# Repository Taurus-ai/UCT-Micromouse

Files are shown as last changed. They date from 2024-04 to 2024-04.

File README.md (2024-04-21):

# UCT-Micromouse
Background
This repository contains the work for the Micromouse Project in the EEE3088F course for 2024. The goal is to design and build two critical subsystems for a maze-solving robot called a micromouse: the power module and the sensing module.

The power module is responsible for powering the robot's motors, charging the battery, and managing power efficiently. It ensures the micromouse has the energy it needs to navigate the maze.

The sensing module acts as the "eyes" of the micromouse, detecting obstacles, walls, and potential paths through the maze using sensors. Without accurate sensing, the robot would be unable to map and solve the maze effectively.

The main challenge of the project will be to adhere to a strict budget.

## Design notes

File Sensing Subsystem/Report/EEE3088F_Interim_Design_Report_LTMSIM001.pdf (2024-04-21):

# Chapter 1

# Subsystem Design

### 1.1 Design Decisions

### 1.1.1 Final Design

The final design is centred around the working of two circuits; the IR-emitter circuit and the IR-receiver circuit, (in order to meet SP04.)
Various configurations were considered for the IR-receiver circuit, particularly configurations involving photo-diodes and photo-transistors. Their trade-offs were compared, and the photo-transistor configuration was chosen.

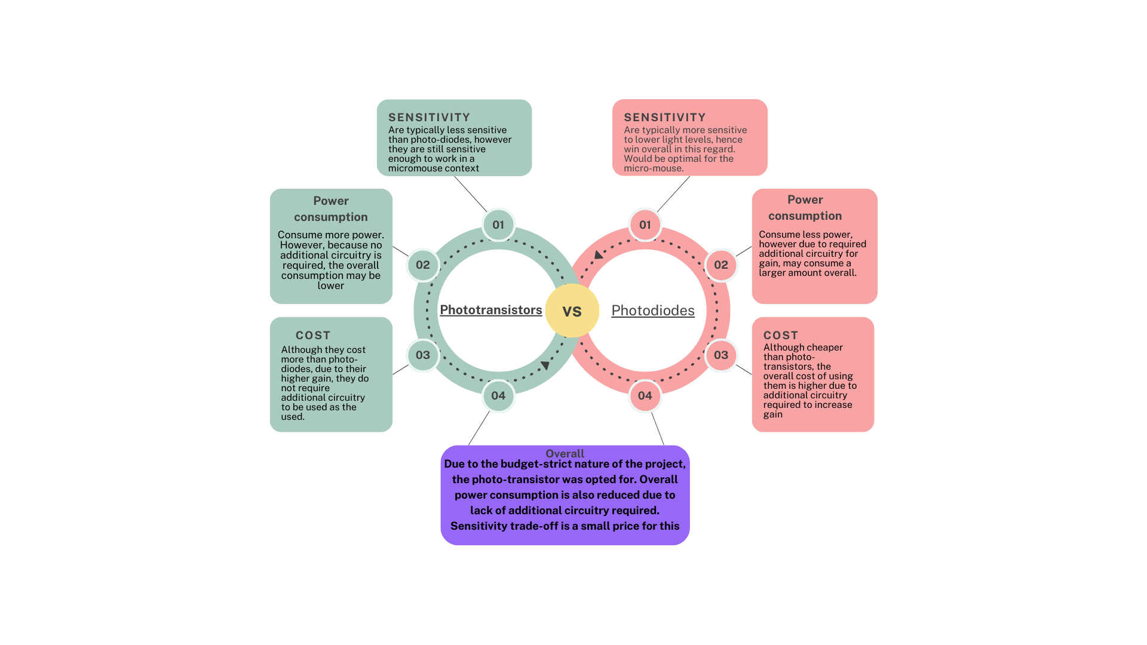
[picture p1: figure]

Figure 1.1: Comparison between phototransistor and photodiode

The choice was made to use the L-51ROPT1D1 phototransistor and OSRAM SFH-4544 IR-LED specifically was due to their spectral matching(940nm), which will ensures maximum signal strength, sensitivity and responsivity as both the receiver and the emitter will be operating at the same wavelengths.

In order to meet SP06 and UR02, the unique design decision to make use of a transistor to act as a switch within the IR-emitter circuit design was made.It will ensure that IR signals are only emitted once a command is given by the MCU, hence allowing for power saving functionality (through the use

1.1. Design Decisions

of code), as well as greater overall control of the circuit.
The decision to use a MOSFET as opposed to the other types of transistors was made due to faster switching speeds, lower conduction losses, and simpler drive circuitry. The drawback was that they are more prone to damage caused by electrostatic charges.
To align with the budget-strict nature of the project, the AO3401A MOSFET P-CH SOT23-3L was chosen.

Capacitors were incorporated into the design in order to stabilize the supply voltage (remove noise) as well as to reduce the turn time on the IR-emitter circuit. These proved to be reasonable trade-offs for the increase in overall cost that they posed. Even then, cheaper capacitors were used to save money.

For saved cost, surface mount resistors were chosen instead of through hole resistors (which are more expensive). The trade off was that these types of resistors are harder to remove and replace from the PCB, which may make things harder to fix if values were miscalculated.

Resistor values were calculated in the figure below:

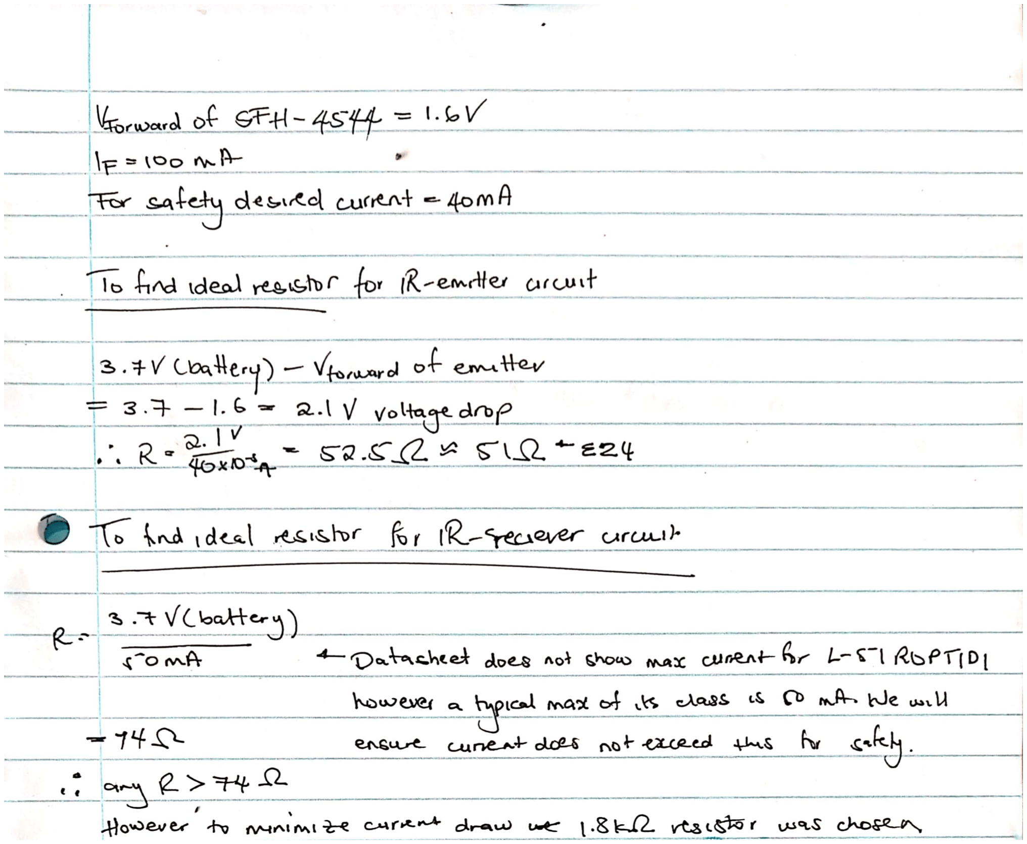
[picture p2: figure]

Figure 1.2: Resistor Value Calculations

If these resistor values are replaced with others, it may result in damage of components on one extreme (too low) or higher current draw on the other extreme, which may cause increased power consumption and hinder UR04.

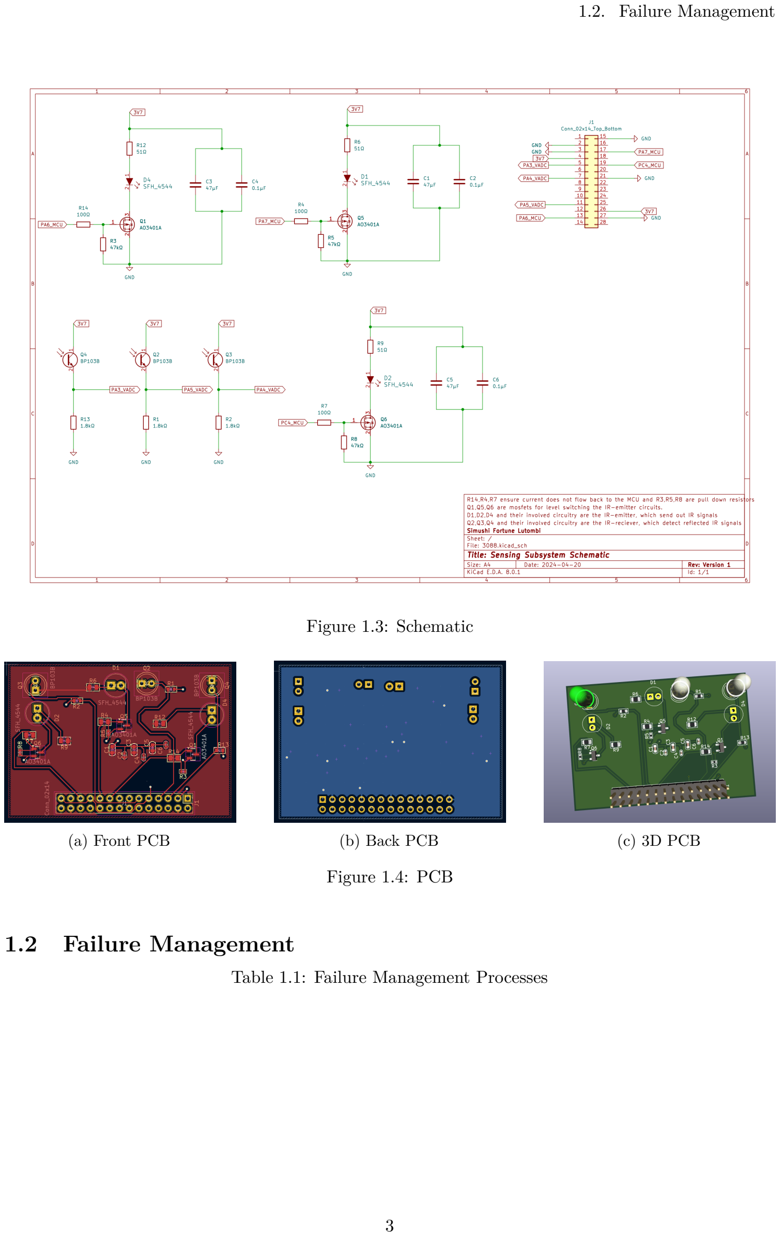
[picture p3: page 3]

1.2. Failure Management

Figure 1.3: Schematic

(a) Front PCB | (b) Back PCB | (c) 3D PCB

Figure 1.4: PCB

### 1.2 Failure Management

Table 1.1: Failure Management Processes

1.3. System Integration and Interfacing
Name | Description
Non-right angle traces | 90° traces were generally avoided to reduce the formation of acid traps during etching
Protective resistors | Various resistors were used to mitigate excessive current from flowing to
| components
Simulation of electrical circuit | The working of the electrical logic of the PCB was tested using Ki-cads inbuilt
ERC functions to ensure that there were no errors in this regard
Design logic testing | Ki-cads inbuilt Design Rule Checking functionality was used to
ensure that there were no obvious design faults, such as short circuits

### 1.3 System Integration and Interfacing

To integrate the subsystem with the rest of the system ....

Table 1.2: Interfacing specifications

Interface | Description | Pins/Output

I001

Sensing Submodule to Microcontroller(MC) for data transfer

- Pin7 to MC-PA4(GPIO)
- Pin11 to MC-PA5(GPIO)
- Pin5 to MC-PA3(GPIO)
- Pin13 to MC-PA6(GPIO)
- Pin17 to MC-PA7
- Pin19 to MC-PC4
- Pin2 to MC-GND
- Pin3 to MC-GND
- Pin15 to MC-GND
- Pin21 to MC-GND
- Pin27 to MC-GND
- Pin4 to MC-Battery
- Pin26 to MC-Battery

1.3. System Integration and Interfacing

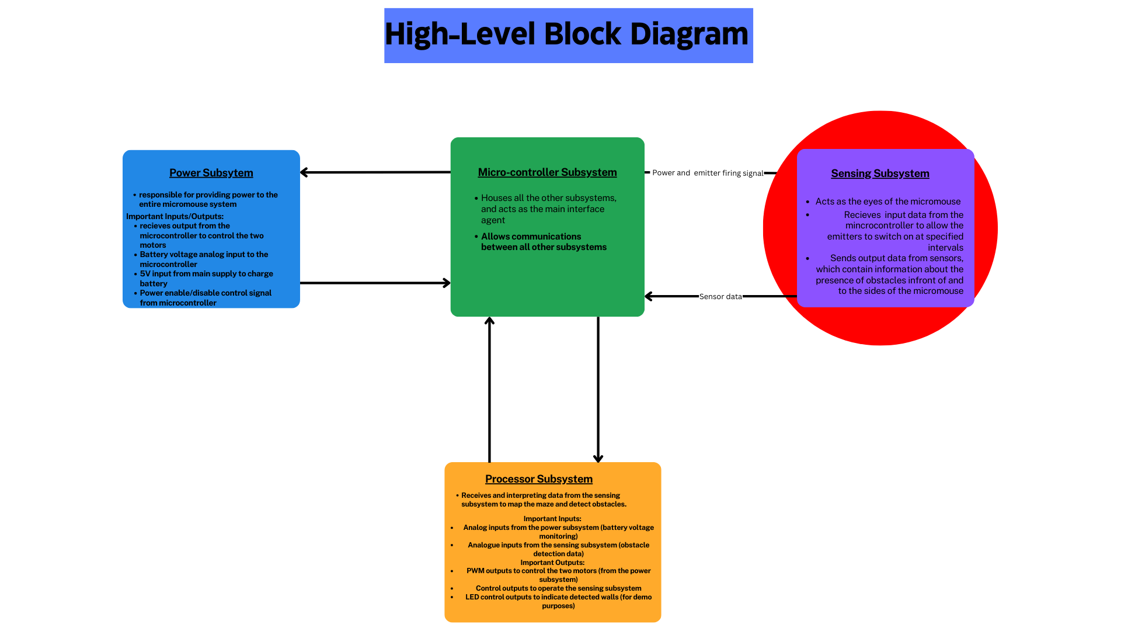
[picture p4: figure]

Figure 1.5: High-level Block Diagram

# Bibliography

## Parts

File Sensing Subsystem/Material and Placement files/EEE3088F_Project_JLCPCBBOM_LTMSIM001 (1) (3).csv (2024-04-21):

Comment | Designator | Footprint | JLCPCB Part #（optional）
P Channel SOT-23 MOSFET | Q1,Q5,Q6 | BP103B | C15127
940nm 5mm Infrared (IR) LED | D1,D2,D4 | AO3401A | C2900370
Thick Film Resistor ±1% 1.8kΩ | R1,R2,R13 | R_0603 | C4177
Thick Film Resistor ±1% 51Ω | R6,R12,R9 | R_0805 | C17738
4.7uF ±20% Multilayer Ceramic Capacitors | C1,C3,C5 | C_0603 | C23733
100nF ±10% Multilayer Ceramic Capacitors | C2,C4,C6 | C_0402 | C14663
Thick Film Resistor ±1% 47kΩ | R3,R5,R8 | R_0402 | C25792
Thick Film Resistors ±1% 100Ω | R4,R14,R7 | R_0805 | C17408
940nm 5mm Phototransistor | Q2,Q3,Q4 | SFH_4544 | C2962773

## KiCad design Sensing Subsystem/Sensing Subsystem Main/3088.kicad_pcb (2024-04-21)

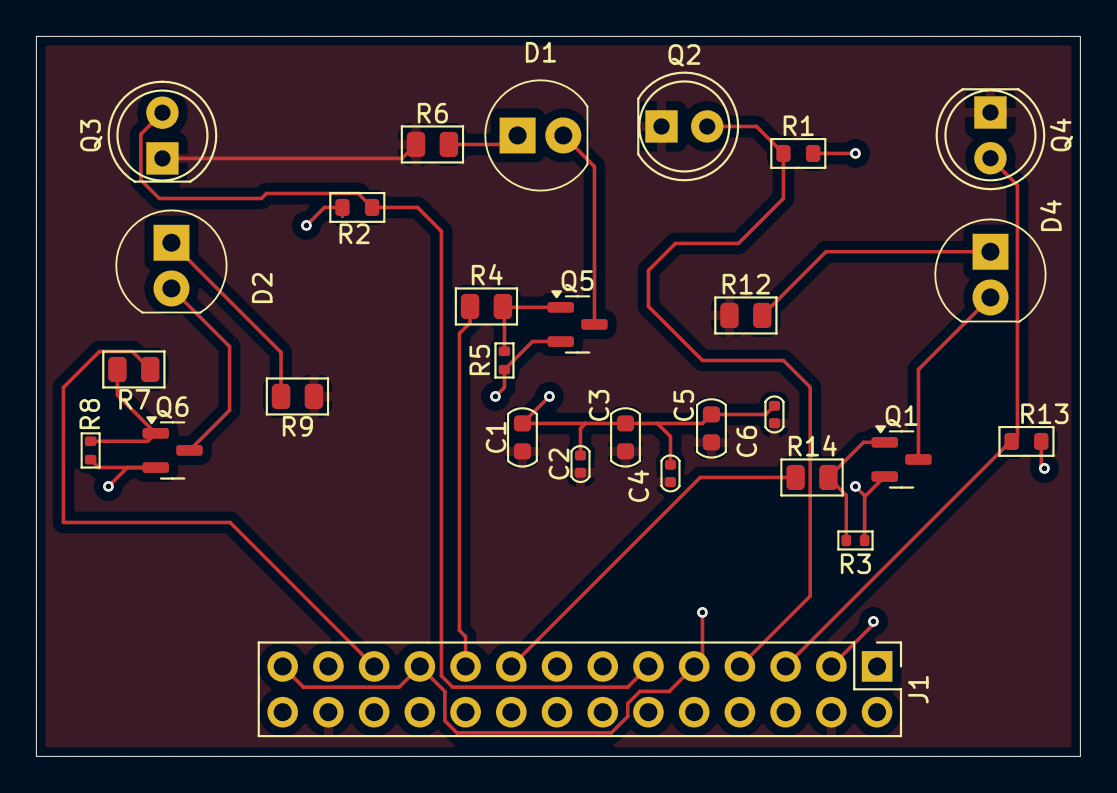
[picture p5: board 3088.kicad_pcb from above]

Board: 2 copper layers, 58.0 x 40.0 mm, 28 parts (0 on the bottom side), 17 nets.

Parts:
C1, C3, C5: C_0603; C_0603_1608Metric
C2, C4, C6: C_0402; C_0402_1005Metric
D1, D2, D4: SFH_4544; LED_5mm_Radial
J1: Conn_02x14; PinHeader_2x14_P2.54mm_Vertical
Q1, Q5, Q6: AO3401A; SOT-23
Q2, Q3, Q4: BP103B; LED_D5.0mm_Clear
R1, R2, R13: R_0603; R_0603_1608Metric
R3, R5, R8: R_0402; R_0402_1005Metric
R4, R6, R7, R9, R12, R14: R_0805; R_0805_2012Metric

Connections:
GND: C1.2, C2.2, C3.2, C4.2, C5.2, C6.2, J1.3, J1.9, J1.15, J1.21, J1.27, Q1.2 (S), Q5.2 (S), Q6.2 (S), R1.2, R2.2, R3.1, R5.1, R8.1, R13.2
MCU: J1.17, R14.1
MCU1: J1.19, R4.1
MCU2: J1.23, R7.1
unnamed: D1.1, R6.2
unnamed: D2.1, R9.2
unnamed: D4.1, R12.2
unnamed: D4.2, Q1.3 (D)
unnamed: Q1.1 (G), R3.2, R14.2
unnamed: D1.2, Q5.3 (D)
unnamed: Q5.1 (G), R4.2, R5.2
unnamed: D2.2, Q6.3 (D)
unnamed: Q6.1 (G), R7.2, R8.2
V_out: J1.5, Q4.2 (E), R13.1
V_out1: J1.7, Q2.2 (E), R1.1
V_out2: J1.11, Q3.2 (E), R2.1
power: C1.1, C2.1, C3.1, C4.1, C5.1, C6.1, J1.4, J1.26, Q2.1 (C), Q3.1 (C), Q4.1 (C), R6.1, R9.1, R12.1

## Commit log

2024-04-07 Create POWER SUBMODULE
2024-04-07 Add files via upload
    This is a bill of mateterials files for the power submodule
2024-04-07 Add files via upload
    Datasheets for the coimponents used in the power submodule design
2024-04-07 Add files via upload
    Kicad files designs for the Power submodule
2024-04-21 Format cleaned up
    [3088-B_Cu.gbr, 3088-B_Mask.gbr, 3088-B_Paste.gbr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]
